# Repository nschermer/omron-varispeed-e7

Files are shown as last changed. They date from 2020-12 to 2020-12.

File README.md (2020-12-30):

# omron-varispeed-e7

Arduino project to communicate with OMRON Varispeed E7 VFD using memobus for my lathe.

## Reason
I have this VFD hooked up to my lathe, because it makes using the lathe much easier to work with. The lathe e-motor also has an electric brake which can be controlled with the VFD (relay). But depending on the job you want to use the mechanical brake (instant stop for thread cutting for example) or decelerate with the VFD (most other work).

To change this, you need to enter the programming menu and change the stopping mode (b1-03), which is doable, but not sexy.

As a small addition I've also added a mode for thread cutting, where you can *boost* the reverse speed, compared to the forward speed. This way you can do a quick return after a long thread cut :sunglasses:.

Furthermore the VFD status is displayed on the LCD and some extra info like the motor power and DC bus voltage.

## MEMOBUS
Memobus is properly described in the manual, it works like RS-485, bit I could not get this working with the existing Arduino libraries, so wrote some code for what was needed to read/write registers in the Varispeed drive.

## Hardware

- OMRON Varispeed E7 (any version will work);
- Arduino pro micro (ATmega32U4 chip, because you can use the serial port for modbus, without interfere the usb-serial connection);
- MAX485 TTL to RS485 module;
- LCD 2004 with I2C interface;
- 20K potentiometer  (10K will work fine as well, but will consume a bit more power) for reference speed;
- Rotary encoder + button for navigating the menu; 
- Power supply: note that modbus on the MAX485 needs **6V** to avoid communication errors. Therefore the MAX is connected to the RAW pin on the Arduino.

## Layout

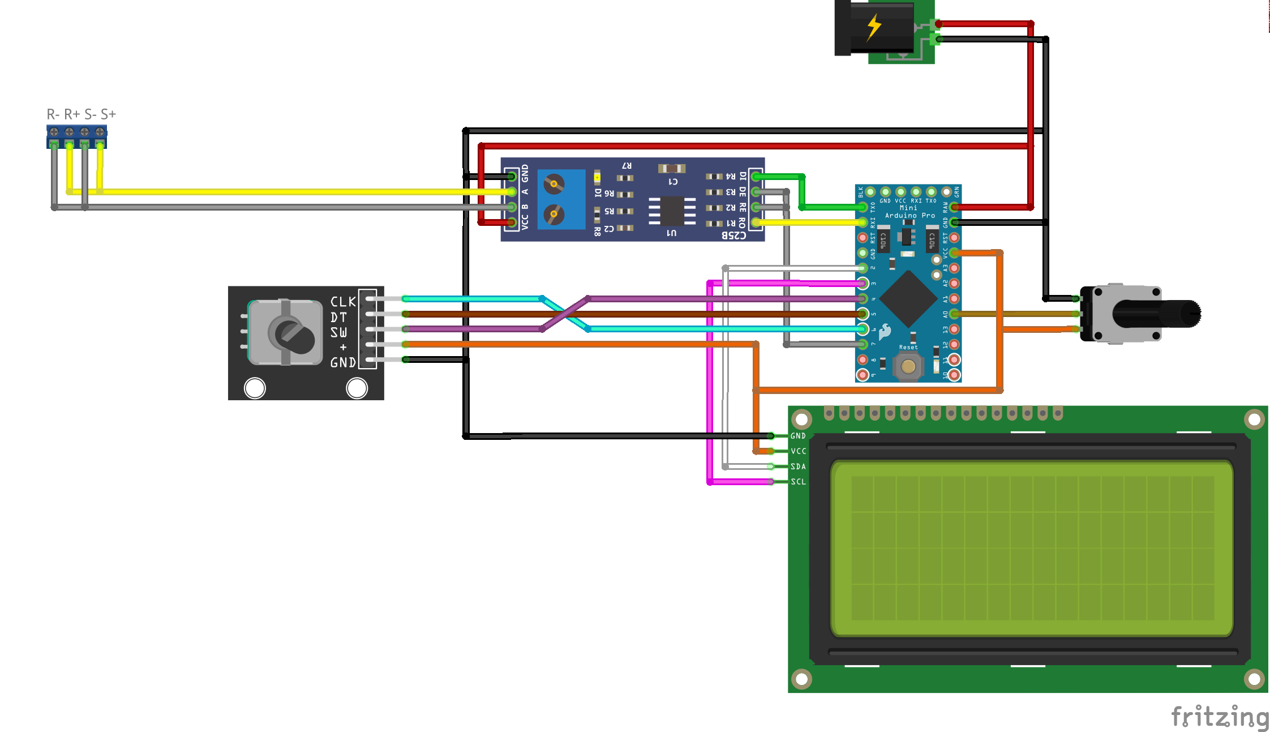
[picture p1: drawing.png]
Board layout


## Setup
- Configure the VFD according to your e-motor;
- Optionally set S1 pin 1 to on for RS-485 termination;
- Configure the MEMOBUS settings according to the settings in the memobus.h header (most are the defaults);
- Speed reference from the VFD using memobus;
- I use the 2-wire setup for forward/reverse, but that up to you;
- Make sure the VFD settings in the main ino match you needs (min/max freq, motor poles, units);
- Don't bother me if it doesn't work.

## How it works
- With the potentiometer you can set the motor speed.
- Push the rotary button to cycle the 3 mode: decelerate, brake (coast down mode on vfd), threading (quick reverse).
- Rotate encoder to change threading reverse speed in this mode.

## Other boards
The code will work with other Arduinos too, but then you need SoftwareSerial. It will take care of this during compilation because I initially used an Uno for testing.

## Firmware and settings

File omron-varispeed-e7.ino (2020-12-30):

#include <Wire.h>

#include "memobus.h"

#include <LiquidCrystal_I2C.h>
#include <Button2.h>   // https://github.com/LennartHennigs/Button2
#include <ESPRotary.h> // https://github.com/LennartHennigs/ESPRotary

/* VFD settings */
#define VFD_HZ_TO_RPM(hz)   ((hz) * 30) /* (Hz x 60 x 2) / number of poles */
#define VFD_MIN_HZ          10
#define VFD_MAX_HZ          100
#define VFD_HZ_UNITS(hz)    (constrain((hz), VFD_MIN_HZ, VFD_MAX_HZ) * 100) /* o1-03 = 0 */

/* Rotory encoder */
#define ROTARY_PIN_CLK  6
#define ROTARY_PIN_DT   5
#define ROTARY_PIN_SW   4
#define ROTARY_CPS      4 /* clicks per step */

/* Analog value filter */
#define KALMAN_ERR_MEASURE 4
#define KALMAN_NOISE       0.01

#define UNUSED __attribute__((unused))

#define INT_NTH_BIT(i,n) (((i) >> (n)) & 0b1)

ESPRotary         encoder(ROTARY_PIN_CLK, ROTARY_PIN_DT, ROTARY_CPS);
Button2           button(ROTARY_PIN_SW);
LiquidCrystal_I2C lcd(0x27, 20, 4);

bool     menu_update = true;
int      mode = 0;
int      ref_frequency = 0;
int      tapping_rev_perc = 150;
int      error_linenr = -1;
int      fail_counter = 8; /* no fail first run */

uint16_t last_inverter_status = 0;
int      last_inverter_ref = -1;
double   last_inverter_kw = -1;
int      last_dc_bus = -1;

/* update timers */
#if MEMOBUS_LOOPBACK
static unsigned long loopbackMillis = 0;
#endif
unsigned long potmeterMillis = 0;
unsigned long statusFastMillis = 0;
unsigned long statusSlowMillis = 0;

void setup() {
  /* usb serial */
  Serial.begin(9600);

  /* serial communication RS485 module */
  memobus_setup();

  /* rotary encoder handling */
  button.setTapHandler(button_click);
  encoder.setLeftRotationHandler(encoder_rotate);
  encoder.setRightRotationHandler(encoder_rotate);

  lcd.init();
  lcd.backlight();
}

void loop () {
  float meas_pot;
  int ref_new;
  char buf[16] = { 0 };
  uint16_t status[8] = { 0 };
  int inverter_ref;
  double inverter_kw;
  int dc_bus;

  button.loop();
  encoder.loop();

  if (menu_update) {
    lcd.clear();
    lcd.setCursor(0, 0);

    switch (mode) {
      case 0:
        lcd.print(F("Mode: Decelerate"));
        break;

      case 1:
        lcd.print(F("Mode: Brake"));
        break;

      case 2:
        lcd.print(F("Mode: Threading"));
        print_tapping ();
        break;
    }

    /* Set stopping mode b1-03 and send enter command */
    if (!memobus_write_register(0x0182, mode == 0 ? 0 : 1)) {
      error_handler(__LINE__);
    } else if (!memobus_write_register(0x910, 0)) {
      error_handler(__LINE__);
    }

    lcd.setCursor(0, 1);
    lcd.print(F("Ref:      rpm"));

    lcd.setCursor(6, 1);
    lcd.print(VFD_HZ_TO_RPM(ref_frequency));

    lcd.setCursor(0, 2);
    lcd.print(F("VFD:  Not connected"));

    menu_update = false;
    last_inverter_status = 0;
    last_inverter_ref = -1;
    last_inverter_kw = -1;
    last_dc_bus = -1;

    /* next round */
    return;
  }

  /* analog value kalman filter update */
  meas_pot = kalman_filter (analogRead(A0));

  /* check if we need to udpate freq */
  if (millis() - potmeterMillis >= 100) {
    ref_new = map(meas_pot, 0, 1023, VFD_MIN_HZ, VFD_MAX_HZ);

    if (ref_frequency != ref_new) {
      /* update value */
      ref_frequency = ref_new;

      /* update setpoint on VFD */
      if (!memobus_write_register(0x0002, VFD_HZ_UNITS(ref_frequency))) {
        error_handler(__LINE__);
      }

      lcd.setCursor(6, 1);
      lcd.print(VFD_HZ_TO_RPM(ref_frequency));
      if (ref_frequency < (1000 / VFD_HZ_TO_RPM(1)))
        lcd.print(" ");

      /* only 1 memobus action per loop() */
      return;
    }

    potmeterMillis = millis();
  }

#if MEMOBUS_LOOPBACK
  /* loopcheck after 80% of CE time expired */
  if (millis() - loopbackMillis >= MEMOBUS_CE_TIME * 0.8) {
    if (!memobus_loopback_test()) {
      error_handler(__LINE__);
    }
    loopbackMillis = millis();
  }
#endif

  if (millis() - statusFastMillis >= 250) {
    /* read status */
    if (memobus_read_register (0x0020, sizeof(status), status)) {

      if (last_inverter_status != status[0]) {
        /* 0x0020 inverter status */
        lcd.setCursor(6, 2);
        if (INT_NTH_BIT (status[0], 3)) {
          lcd.print(F("Fault   "));
        } else if (INT_NTH_BIT (status[0], 0)) {
          lcd.print(INT_NTH_BIT (status[0], 1) ? F("Reverse ") : F("Forward "));
        } else if (INT_NTH_BIT (status[0], 2)) {
          lcd.print(F("Ready   "));
        } else {
          lcd.print(F("Unknown "));
        }

        /* tapping mode */
        if (mode == 2) {
          /* forward to reverse speed */
          if (INT_NTH_BIT (status[0], 1)) {
            ref_new = ref_frequency * tapping_rev_perc / 100;
          } else {
            ref_new = ref_frequency;
          }

          /* update setpoint on VFD */
          if (!memobus_write_register(0x0002, VFD_HZ_UNITS(ref_new))) {
            error_handler(__LINE__);
          }
        }

        last_inverter_status = status[0];
      }

      /* Output frequency */
      inverter_ref = min (status[4] / 100, 999);
      if (last_inverter_ref != inverter_ref) {
        lcd.setCursor(14, 2);
        snprintf(buf, sizeof(buf), "%3dHz", inverter_ref);
        lcd.print(buf);

        last_inverter_ref = inverter_ref;
      }

      /* Output power */
      inverter_kw = (double) min (status[7], 99) / 10;
      if (last_inverter_kw != inverter_kw) {
        lcd.setCursor(6, 3);
        lcd.print(inverter_kw, 1);
        lcd.print(F("kW"));

        last_inverter_kw = inverter_kw;
      }

      /* reset fail counter */
      fail_counter = 0;
    } else {
      /* count fails */
      fail_counter++;

      if (fail_counter == 8) {
        /* force menu update (clear) */
        menu_update = true;
      }
    }

    statusFastMillis = millis();

    /* only 1 memobus action per loop() */
    return;
  }

  if (millis() - statusSlowMillis >= 1000) {
    /* read status */
    if (memobus_read_register (0x0031, 1, status)) {
      dc_bus = min(status[0], 999);
      if (last_dc_bus != dc_bus) {
        lcd.setCursor(14, 3);
        snprintf(buf, sizeof(buf), "%3dVDC", dc_bus);
        lcd.print(buf);

        last_dc_bus = dc_bus;
      }
    }

    /* debug helper (0 clear line, -1 no action, >0 print number) */
    if (error_linenr != -1) {
      lcd.setCursor(0, 3);
      if (error_linenr > 0) {
        lcd.print(error_linenr);
        error_linenr = 0;
      } else {
        lcd.print(F("   "));
        error_linenr = -1;
      }
    }

    statusSlowMillis = millis();
  }
}

float
kalman_filter(int measured) {
  static float err_estimate = KALMAN_ERR_MEASURE;
  static float last_estimate = measured;
  float kalman_gain;
  float current_estimate;

  kalman_gain = err_estimate / (err_estimate + KALMAN_ERR_MEASURE);
  current_estimate = last_estimate + kalman_gain * (measured - last_estimate);
  err_estimate =  (1.0 - kalman_gain) * err_estimate + fabs(last_estimate - current_estimate) * KALMAN_NOISE;
  last_estimate = current_estimate;

  return current_estimate;
}

void error_handler(int line) {
  error_linenr = line;

  if (Serial) {
    Serial.print(F("Error line "));
    Serial.println(line);
  }
}

void print_tapping () {
  char buf[8] = { 0 };

  lcd.setCursor(16, 0);
  snprintf (buf, sizeof(buf), "%3d%%", min (tapping_rev_perc, 999));
  lcd.print(buf);
}

void encoder_rotate(UNUSED ESPRotary & r) {
  if (mode == 2) {
    tapping_rev_perc += encoder.getDirection() == RE_LEFT ? -10 : 10;

    if (tapping_rev_perc < 50)
      tapping_rev_perc = 50;
    if (tapping_rev_perc > 500)
      tapping_rev_perc = 500;

    print_tapping ();
  }
}

void button_click(UNUSED Button2 & b) {
  mode++;

  if (mode > 2)
    mode = 0;

  menu_update = true;
}

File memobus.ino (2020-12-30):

#include "memobus.h"

/* SoftwareSerial or Serial1 (HW serial) on the MEGA32U4 boards */
#if defined(__AVR_ATmega32U4__)
#define RS485 Serial1
#else
#define RS485_SW_SERIAL
#include <SoftwareSerial.h>
SoftwareSerial RS485(RS485_RX, RS485_TX);
#endif

#define RS485_TRANSMIT HIGH
#define RS485_RECEIVE  LOW

/* memobus message spacing timer */
unsigned long MemobusSpacingTimer = 0;

void memobus_setup () {
  pinMode(RS485_RTS, OUTPUT);
  RS485.begin(MEMOBUS_BITRATE);
  RS485.setTimeout(MEMOBUS_TIMEOUT);
  while (!RS485);
}

#if 0
void memobus_print_buffer(byte * buf, int len) {
  for (byte i = 0; i < len; i++ ) {
    Serial.print(buf[i], HEX);
    Serial.print(F(" "));
  }
  Serial.println();
}
#endif

void memobus_check_spacing_delay() {
  unsigned long expired;

  /* check if we need to delay to make sure the new command is
     MEMOBUS_WAIT_TIME after the last response message */
  expired = millis() - MemobusSpacingTimer;
  if (expired < MEMOBUS_WAIT_TIME) {
    delay(MEMOBUS_WAIT_TIME - expired);
  }
}

bool memobus_write_register(uint16_t address, uint16_t data) {
  byte msg[11];
  byte buf[8] = { 0 };
  uint16_t quantity = 1; /* nr of registers */
  uint16_t crc;
  int retval;

  msg[0] = MEMOBUS_SLAVE_ID;
  msg[1] = 0x10; /* write memory */
  msg[2] = highByte(address);
  msg[3] = lowByte(address);
  msg[4] = highByte(quantity);
  msg[5] = lowByte(quantity);
  msg[6] = lowByte(quantity * 2); /* nr high/low data fields */
  msg[7] = highByte(data);
  msg[8] = lowByte(data);

  crc = memobus_msg_crc16 (msg, 9);
  msg[9] = lowByte(crc); /* crc has swapped bytes */
  msg[10] = highByte(crc);

  /* check if we need to sleep */
  memobus_check_spacing_delay();

  /* send request */
  digitalWrite(RS485_RTS, RS485_TRANSMIT);
  RS485.write(msg, sizeof(msg));
  RS485.flush();

  delay(MEMOBUS_WAIT_TIME);

  /* read reply */
  digitalWrite(RS485_RTS, RS485_RECEIVE);
  retval = RS485.readBytes(buf, sizeof (buf));
  if (retval < (int) sizeof (buf)) {
    error_handler(__LINE__);
    return false;
  }

  /* store new last response timestamp */
  MemobusSpacingTimer = millis();

  /* check for error */
  if (buf[0] != MEMOBUS_SLAVE_ID || buf[1] == 0x90) {
    error_handler(__LINE__);
    return false;
  }

  /* validate reply */
  crc = memobus_msg_crc16 (buf, sizeof(buf) - 2);
  if (lowByte(crc) != buf[6] || highByte(crc) != buf[7]) {
    error_handler(__LINE__);
    return false;
  }

  /* check if all values are written (first 6 fields) */
  return memcmp(msg, buf, 6) == 0;
}

bool memobus_read_register(uint16_t start_address, uint16_t quantity, uint16_t *ret_status) {
  byte msg[8];
  uint16_t crc;
  byte buf[64] = { 0 };
  size_t bufsize;
  uint16_t i;
  uint16_t offset;
  int retval;

  msg[0] = MEMOBUS_SLAVE_ID;
  msg[1] = 0x03; /* read memory */
  msg[2] = highByte(start_address);
  msg[3] = lowByte(start_address);
  msg[4] = highByte(quantity);
  msg[5] = lowByte(quantity);

  crc = memobus_msg_crc16 (msg, 6);
  msg[6] = lowByte(crc); /* crc has swapped bytes */
  msg[7] = highByte(crc);

  /* buffer reply size (response message has 5 items + 2 for each register) */
  bufsize = 5 + 2 * quantity;

  /* check if our static buffer is big enough this way we avoid malloc/free */
  if (bufsize > sizeof(buf)) {
    error_handler(__LINE__);
    return false;
  }

  /* check if we need to sleep */
  memobus_check_spacing_delay();

  /* send request */
  digitalWrite(RS485_RTS, RS485_TRANSMIT);
  RS485.write(msg, sizeof(msg));
  RS485.flush();

  delay(MEMOBUS_WAIT_TIME);

  /* read reply */
  digitalWrite(RS485_RTS, RS485_RECEIVE);
  retval = RS485.readBytes(buf, bufsize);
  if (retval < (int) bufsize) {
    //error_handler(__LINE__);
    return false;
  }

  /* store new last response timestamp */
  MemobusSpacingTimer = millis();

  if (buf[0] != MEMOBUS_SLAVE_ID || buf[1] == 0x83) {
    error_handler(__LINE__);
    return false;
  }

  /* validate reply */
  crc = memobus_msg_crc16 (buf, bufsize - 2);
  if (lowByte(crc) != buf[bufsize - 2] || highByte(crc) != buf[bufsize - 1]) {
    //error_handler(__LINE__);
    return false;
  }

  /* store data in return register */
  for (i = 0; i < quantity; i++) {
    offset = i * 2 + 3;
    /* merge higher and lower bit in integer */
    ret_status[i] = buf[offset] << 8 | buf[offset + 1];
  }

  return true;
}

#if MEMOBUS_LOOPBACK
boolean memobus_loopback_test(void) {
  uint16_t crc;
  byte buf[8] = {0 };
  byte msg[8];
  long rnd;
  int retval;

  /* we insert random data in the msg */
  rnd = random();

  /* create the loopback request */
  msg[0] = MEMOBUS_SLAVE_ID;
  msg[1] = 0x08; /* loopback test */
  msg[2] = highByte(rnd);
  msg[3] = lowByte(rnd);
  msg[4] = highByte(rnd + 1);
  msg[5] = lowByte(rnd + 1);

  /* complete crc */
  crc = memobus_msg_crc16(msg, 6);
  msg[6] = lowByte(crc); /* crc has swapped bytes */
  msg[7] = highByte(crc);

  /* check if we need to sleep */
  memobus_check_spacing_delay();

  /* send request */
  digitalWrite(RS485_RTS, RS485_TRANSMIT);
  RS485.write(msg, sizeof(msg));
  RS485.flush();

  delay(MEMOBUS_WAIT_TIME);

  /* read reply */
  digitalWrite(RS485_RTS, RS485_RECEIVE);
  retval = RS485.readBytes(buf, sizeof(buf));
  if (retval < (int) sizeof(buf)) {
    error_handler(__LINE__);
    return false;
  }

  /* store new last response timestamp */
  MemobusSpacingTimer = millis();

  /* check for error */
  if (buf[0] != MEMOBUS_SLAVE_ID || buf[1] == 0x90)
    return false;

  /* with loopback; message and reply are identical */
  return memcmp(msg, buf, sizeof (buf)) == 0;
}
#endif

uint16_t memobus_msg_crc16(byte * buf, size_t len)
{
  uint16_t crc = 0xFFFF;

  for (size_t pos = 0; pos < len; pos++) {
    crc ^= (uint16_t) buf[pos];       // XOR byte into least sig. byte of crc

    for (int i = 8; i != 0; i--) {    // Loop over each bit
      if ((crc & 0x0001) != 0) {      // If the LSB is set
        crc >>= 1;                    // Shift right and XOR 0xA001
        crc ^= 0xA001;
      } else {                        // Else LSB is not set
        crc >>= 1;                    // Just shift right
      }
    }
  }
  // Note, this number has low and high bytes swapped, so use it accordingly (or swap bytes)
  return crc;
}

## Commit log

2020-12-30 Add kalman filter
2020-12-30 Add schema
    [drawing.fzz]
2020-12-30 Avoid lcd prints because they are slow
    [memobus.ino, omron-varispeed-e7.ino]
